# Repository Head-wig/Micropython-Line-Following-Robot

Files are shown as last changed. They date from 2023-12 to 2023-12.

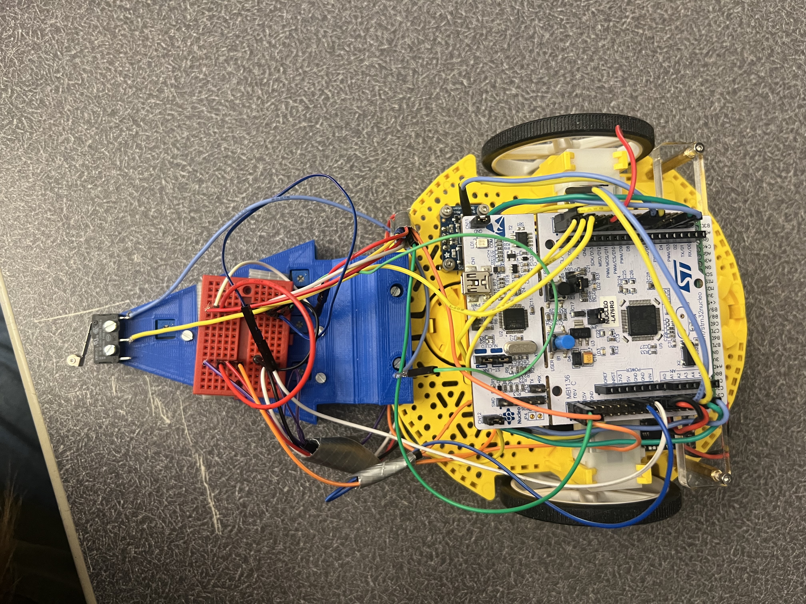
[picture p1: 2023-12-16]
Media/IMG_5954.jpg

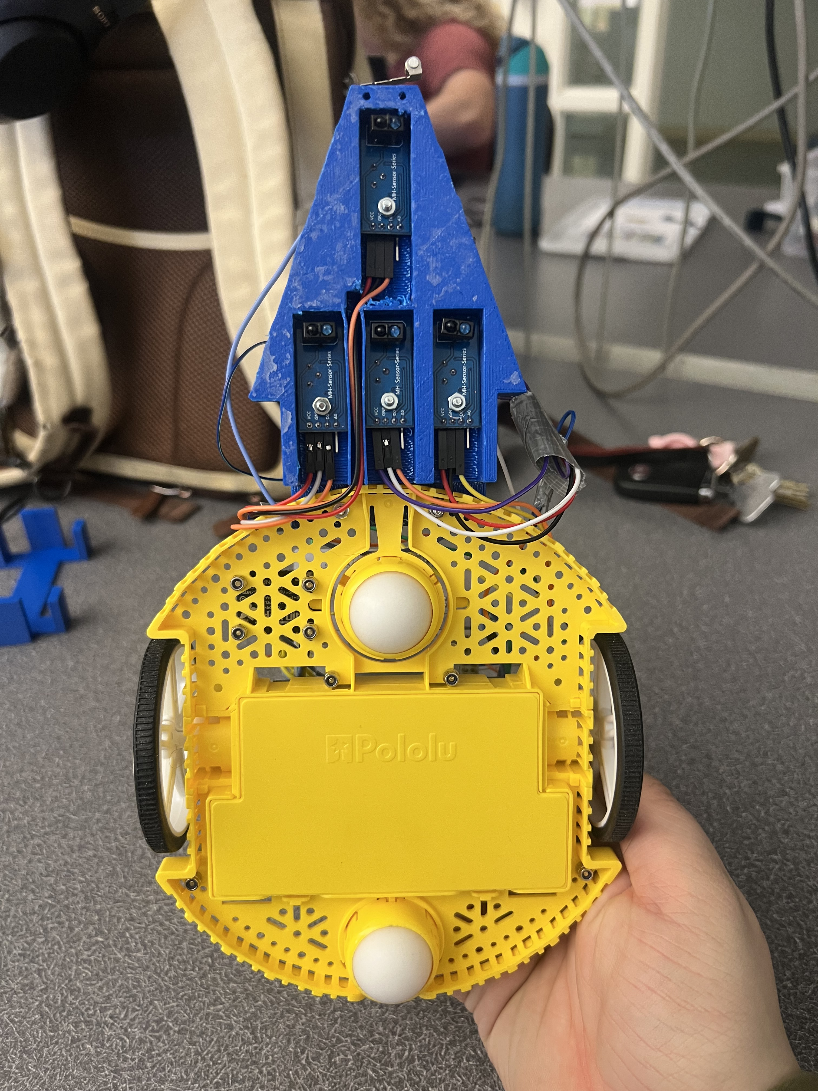
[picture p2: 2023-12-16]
Media/IMG_5957.jpg

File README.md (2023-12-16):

# Micropython Line Following Robot 
The goal of this project was to create a robot on the romi platform controlled by a Nucleo l476rg running micropython that can be activated using the user button on the Nucleo, follow a 1/4'' line, detect obstacles, and return to start potion after completing any given course. This was accomplished by mounting four TCRT5000 IR Sensors to the front of the romi and one limit switch in order to detect any obstacle that may be in the path of the robot.  The data from each sensor was read at a 25ms interval and was used to determine which movements to make based off of predetermined states. 

# Contents
 - [Romi Setup](#romi-setup) 
 - [Code Structure](#code-structure)
 - [Results](#results) 
 - [Known Bugs](#known-bugs)
 - [Future Work](#future-work)
 - [BOM](#billofmaterials)

# Romi Setup
To prepare the romi, connect wires from the four IR sensors, the motor drivers, the limit switch and the breadboard as described in the table below. This table will also contain information that is pertinent to the function of each pin in the classes provided.

|Function|Pin |Mode|Pull|
|--|--|--|--
| Right Motor  PWM|B8|PWM|-|
| Right Motor  DIR|A4|OUT_PP|-|
| Right Motor  SLP|B0|OUT_PP|-| 
| Left Motor  PWM|C8|PWM|-|
| Left Motor  DIR|A10|OUT_PP|-| 
| Left Motor  SLP|B3|OUT_PP|-|  
| IR  Left Digital Out  |C9|IN|-|
| IR  Front Digital Out |C11|IN|-|
| IR  Back Digital Out |C12|IN|-
| IR  Right Digital Out |C10|IN|-|
| Limit Switch Out |B9|IN|PULL_DOWN|
| Bread Board 3.5V Lane | 3.5V |-|-|
| Bread Board Ground Lane |GND|-|-|

Once the pins are correctly connected, install the sensor mount provided in the Models folder. As shown below this model can be connected to the romi using two M2.5 bolts and nuts. The IR sensors can then be install with one M2.5 bolt each. while installing the IR sensors use the built in channel to route the connecting wires to the breadboard and Nucleo respectively. The VCC and GND pins from each sensor should connect to breadboard's 3.5V and ground lanes which can be mounted any place on the romi and secured using double sided tape. Finally,  attach the limit switch to the front of the romi with two additional M2.5 bolts. These two bolts will tap into the material of the print and therefore not need nuts. 
SensorMount

# Code Structure
As stated in the introduction, this code uses a myriad of different sensor states to determine how the robot will move. Below is the state transition diagram depicting the finite state machines used to model the behavior of romi. When first powered on the robot will move to the Off Mode state, as the Start_Button variable initializes as zero. Once the user button is pressed Start_Button is set to one and the code moves to Line Sensors Hub state. In this state it reads all of the sensors and compares them to each of the sensor states.  

Once the corresponding sensor state is found the code will transition to either Pivot state or directly to the Set Duty Cycle state if the robot is going to continue moving forward. Once the Set Duty Cycle has completed it will return to the Button Check state and restart the process. While in the pivot state the code checks the front sensor value, if this value is equal to one, the code effectively returns to the Line Sensor hub state in order to start moving forward again.

 If at any point the limit switch at the front of the robot is depressed the code will stop what its doing and move to the Obstacle Maneuver state. In this state the robot will back up, turn so its parallel to the obstacle and move in an arch until its on the other side of the obstacle at which point the code will return to Button check state and subsequently the Line Sensor Hub State in order to find the line and continue on its path. 

Appa FSM
One last function of this code is the ability to stop the romi at any point by clicking the user button which will transition the code into the Off Mode state. The only time this function will not work is during the Obstacle Maneuver state. 
# Results
When tested, romi completed the course that had been laid out for it in only one minute and four seconds. Below is the video of this test.  Due to time constraints the ability to return to the robots starting position, and a more complex obstacle maneuver algorithm were not added. 

(https://youtu.be/NFez8l3HVpM)

Romi1

# Known Bugs
This build does have a few bugs that this section hopes to address. The first issue is that the TCRT5000 IR Sensors only work on specific surfaces. If the surface is too reflective the sensors will get false readings which will lead the robot off course. Another issues with these sensors is that they can have some sort of malfunction that causes a  much longer response time. This issue comes on without warning and has no current solution. During the building and testing of this romi at least two sensors were replaced due to this issue. 

Another issues faced unrelated to the sensors was the way the Nucleo board interacted with Mac laptops. When loading scripts onto the Nucleo the micropython installation could get corrupted, loosing all files stored on the Nucleo, and necessitating the firmware to be re-flashed 

# Future Work

 - Add a function that will allow romi to return to its starting position using an IMU 
 - Increase compatibility with reflective materials
 - Add more sensors to increase consistency on dashed and curved lines
 - Smooth our turning by either introducing a turning state, changing the way romi pivots, or introducing A PID controller to our motors 

# BOM

| Items |Quantity  |
|--|--|
|Nucleo l476rg | 1 |
|Shoe Of Brian |1
|Romi kit|1
|Limit Switch |1
|Breadboard |1
|TCRT5000 IR Sensors |4
|Pack of assorted wires|1 
|Pack of heat shrink | 1
|Roll of filament |1
|M2.5 Screws | 8
|M2.5 Nuts | 6
|Shoe Of Brian mounting kit | 1

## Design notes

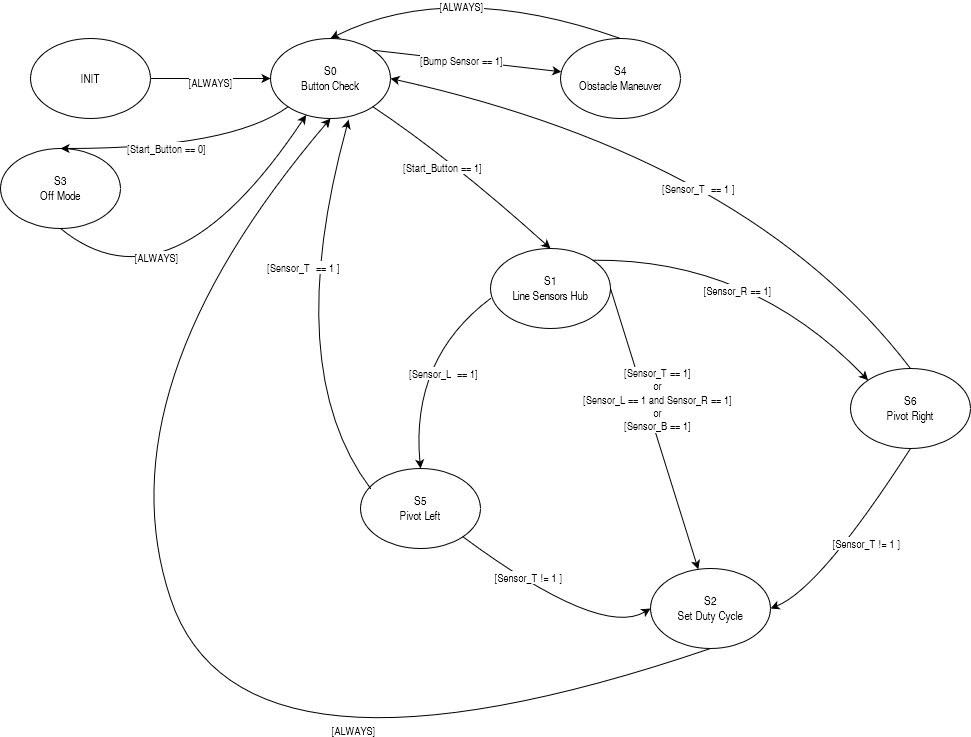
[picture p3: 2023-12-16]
Media/Appa's FSM.drawio(1).png

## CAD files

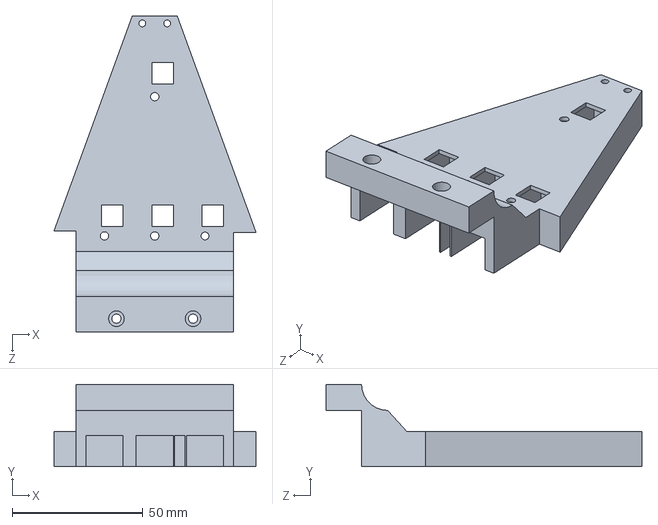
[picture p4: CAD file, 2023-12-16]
Models/RomiSensorsMount.SLDPRT
77.1 x 31.5 x 120.5 mm

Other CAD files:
Models/RomiSensorsMount.STL

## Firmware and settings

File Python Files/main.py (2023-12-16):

import task_share
import cotask
import gc

from appa_brain import appa_brain # controller Task
# from appa_return import appa_return # Predicting what path to take

Appa_Mode = task_share.Share('f',"Appa's Mode")
Left_Wheel_RPM = task_share.Share('f',"RPM of the left wheel")
Right_Wheel_RPM = task_share.Share('f',"RPM of the Right wheel")
X_Distance = task_share.Share('f',"appa x distance away form the finish line")
Y_Distance = task_share.Share('f',"appa x distance away form the finish line")
DEBUG_VAL = task_share.Share('f', "Intertask Debug Value") # Giv Debug


# Create an object to pass in the cotask
CONT = appa_brain(Appa_Mode, Left_Wheel_RPM, Right_Wheel_RPM, X_Distance, Y_Distance, DEBUG_VAL)
# RETURN = appa_return(Appa_Mode, Left_Wheel_RPM, Right_Wheel_RPM, X_Distance, Y_Distance, DEBUG_VAL)

# Put the object into the cotask 
CONT_cotask = cotask.Task(CONT.run, "appa's brain", priority = 1, period = 25)
# RETURN_cotask = cotask.Task(RETURN.run, "appa returns home", priority = 0, period = 2)

# Append the newly created task to the task list

cotask.task_list.append(CONT_cotask)
# cotask.task_list.append(RETURN_cotask)

# Run the scheduler
while True:
    cotask.task_list.pri_sched()
        

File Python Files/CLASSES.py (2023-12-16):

from pyb import Pin,Timer
from time import sleep_ms, ticks_ms, ticks_diff
from array import array
import micropython
from machine import I2C
micropython.alloc_emergency_exception_buf(100)

def Convert_byte(byte_data): # Convert data into one readable integer
    integer_value = 0
    
    for byte in byte_data:
        integer_value = (integer_value << 8) | byte
    return integer_value  

class Motor:
    '''!@brief A driver class for one channel of the L6206.
    @details Objects of this class can be used to apply PWM to a given
    DC motor on one channel of the L6206 from ST Microelectronics.
    '''

    def __init__ (self, PWM_tim, IN1_pin, IN2_pin, EN_pin ):
        '''!@brief Initializes and returns an object associated with a DC motor.
        '''
        # Creates a pin object from the enable pin specified as an input parameter, and then stores the pin object in a calss attributes
        self.timer = PWM_tim
        self.pwm_1 = PWM_tim.channel(3, pin = IN1_pin, mode =Timer.PWM,  pulse_width_percent = 0)
        self.Dir = Pin(IN2_pin, mode = Pin.OUT_PP)
        self.EN = Pin(EN_pin, mode = Pin.OUT_PP)
        
 
    def set_duty (self, duty):
        '''!@brief Set the PWM duty cycle for the DC motor2
        @details This method sets the duty cycle to be sent
        to the L6206 to a given level. Positive values
        cause effort in one direction, negative values
        in the opposite direction.
        @param duty A signed number holding the duty
        cycle of the PWM signal sent to the L6206
        '''
        # IN2 stays constant and pwm_1 is fluctuating values wise
       
        if(duty > 100):
            duty = 100
        elif(duty < -100):
            duty = -100
        # turns on pwm constantly
       
        if duty >= 0:
            self.pwm_1.pulse_width_percent(abs(duty))
            self.Dir.low()
        elif duty < 0:
            self.pwm_1.pulse_width_percent(abs(duty))
            self.Dir.high()
            
    
   
    def enable (self):
        '''!@brief Enable one channel of the L6206.
        @details This method sets the enable pin associated with one
        channel of the L6206 high in order to enable that
        channel of the motor driver.
        '''
        self.EN.high()
        
    def disable (self):
        self.EN.low()
                                
   
class Encoder:

    '''!@brief Interface with quadrature encoders

    @details Objects of this class can be used to read quadrature encoder,
    allowing the position and the change in position to be seen, thereby velocity
    as well.

    '''

    def __init__(self, enc_timer, channelA_Pin, channelB_Pin):
        '''!@brief Constructs an encoder object
        @details This method initializes the class and reset all input parameters
         The reload value and prescale value are set.
        @param enc_timer set up the timer for the channel
        @param channelA_Pin set up the serial communication for channel A
        @param channelB_Pin set up the serial communication for channel A
        '''

        #self.AR = 256*4*16 - 1
        self.AR = 1440 - 1
        self.PS = 0
        self.Delta = 0
        self.position = 0
        self.value = 0
        self.time =  Timer(enc_timer, period = self.AR, prescaler = self.PS)
        self.channelA = self.time.channel(1, pin = channelA_Pin, mode = Timer.ENC_AB)
        self.channelB = self.time.channel(2, pin = channelB_Pin, mode = Timer.ENC_AB)
        self.lastvalue = self.time.counter()

    def update(self):
        '''!@brief Updates encoder position and delta
        @details Get current position from encoder read. If the difference betweeen
        the current value and the last value to be greater than 15000, add the
        auto reload value to the position then subtract the previous position value.
        Otherwise, subtract current position by the previous position for delta.
        Then,current position is saved as the previous position for the next loop cycle
        '''
        self.value = self.time.counter()
        self.Delta = self.value - self.lastvalue
        if self.Delta > (self.AR + 1)//2:
            self.Delta -= self.AR + 1
        elif self.Delta < -(self.AR + 1)//2:
            self.Delta += self.AR +1
       
        self.lastvalue = self.value
       
        self.position = self.position + self.Delta
       
        pass

    def get_position(self):
        '''!@brief Gets the most recent encoder position
        @detaelf.NewVal ils Get the numerical result from update() and print value
        @return printed motor position
        '''
        print(self.position)
       
   
    def get_delta(self):
        '''!@brief Gets the most recent encoder delta
        @details Get the numerical result from update() and print delta
        @return printed motor position difference
        '''
        print(self.Delta)

    def zero(self):
        '''!@brief Resets the encoder position to zero
        @details reset the delta, position, and last position value of
        the motor to zero
        '''
        self.Delta = 0
        self.postion = 0
        self.value = 0
        pass
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
